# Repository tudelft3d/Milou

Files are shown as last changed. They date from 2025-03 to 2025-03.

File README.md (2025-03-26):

# Milou: a low-cost open-source line-following robot to study indoor air



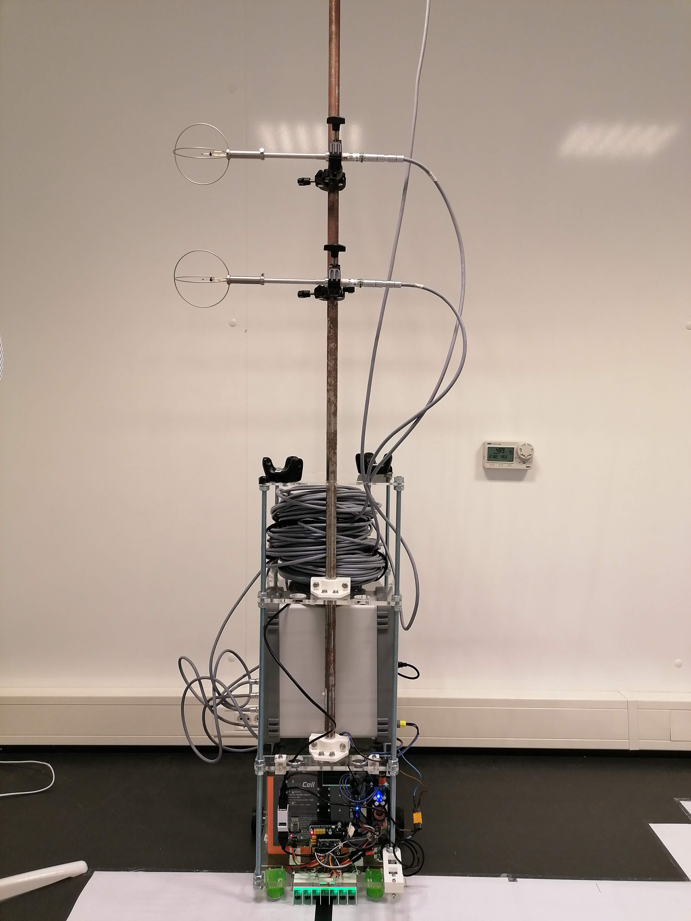
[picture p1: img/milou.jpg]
Milou


Milou is a low-cost line-following robot that automates indoor measurements with low interference. She follows a line and stops at sampling points to measure.
This repository contains the blueprints to build Milou, the code to run and operate it, and the code to post-process the data from a measurement campaign that we did.

This repository accompanies the paper [Milou: a low-cost open-source line-following robot to study indoor air](TO BE PUBLISHED).

## Description of directories

1. `building_milou`: contains the drawings to laser cut and 3d print all parts of Milou in `drawings`, the Arduino code needed to run Milou in `milou_line_following`, and the code needed to connect Milou to a computer remotely in `rp_to_mu_connection`.
2. `postprocessing`: contains three Python files that use the data from this [4TU repository](https://doi.org/10.4121/41307b71-2096-4a31-82ba-f523a18c109a). requirements.txt contains the dependencies to run the python code.

## Parts
The following is a list of all the parts we used to build Milou.
Equivalent parts are also possible.

| Parts 							| Quantity |
| --- 							| ---|
| Arduino Nano Every					| 1 |
| Raspberry Pi Zero W					| 1 |
| MG996R Servo motors 					| 2 |
| ⌀ 6 mm stainless steel rod (1 m long. Use it to make 2 13 cm shafts from motors to wheels) 		 				| 1 |
| 6 mm to 6 mm coupler 					| 2 |
| Ball bearing (⌀ 6 mm inner and ⌀ 19 mm outer) 					| 2 |
| 50 mm ⌀ Aluminum wheel (we needed two on each side to carry the weight)					| 4 |
| Heavy duty castor balls				| 2 |
| TCRT5000 Tracking Sensor Module 	| 7 |
| 12V LiFePO4 battery (38Ah)			| 1 |
| Switch button							| 1 |
| HC-06 Bluetooth module				| 1 |
| ⌀ 10 mm threaded stainless steel rod (1 m long)| 4 |
| ⌀ 20 mm hollow tube (1.75 m long)		| 1 |
| Step-down converter 12 V to 9V (200W)	| 1 |
| Step-down converter 12 V to 5V (5A)	| 2 |

And a lot of wires, screws, nuts, rings, and spacers.
We also used busbars to distribute the power from the battery to the various components.

The rest of the parts are laser cut or 3d printed (see drawings folder).

Below is the wiring scheme of Milou's electrical components.
Circuit board

## Acknowledgements
We want to acknowledge the following [Instructables](https://www.instructables.com/Line-Follower-Robot-PID-Control-Android-Setup/) post that helped build Milou.

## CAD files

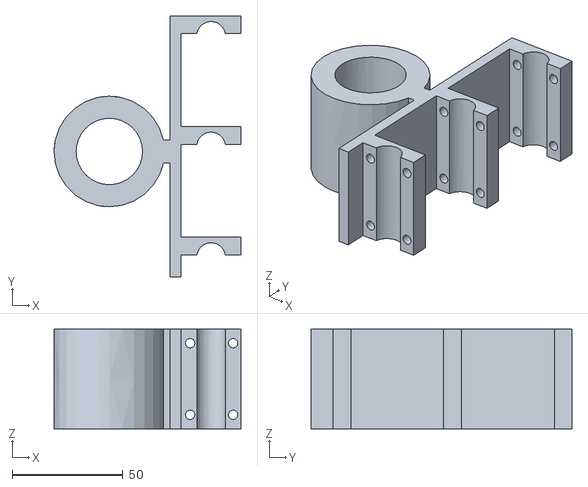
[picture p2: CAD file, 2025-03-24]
building_milou/drawings/probes_holder_bigger_handle.stl
84.5 x 118.0 x 45.0

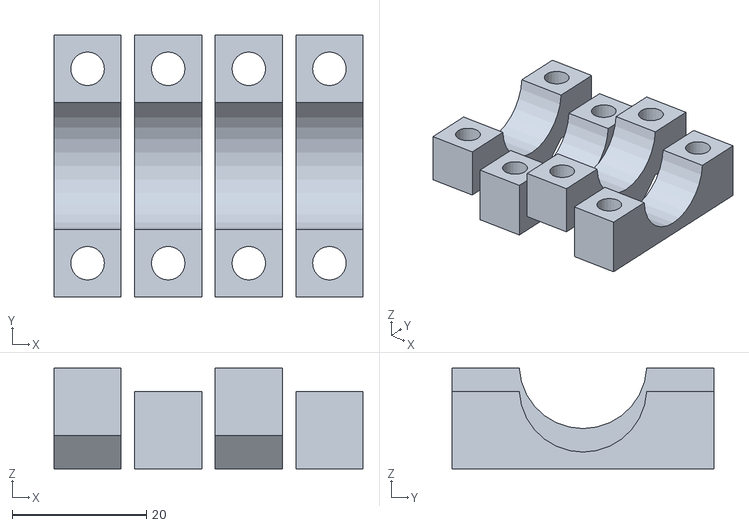
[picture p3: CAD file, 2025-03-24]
building_milou/drawings/pillow_block.stl
46.0 x 38.9 x 15.0

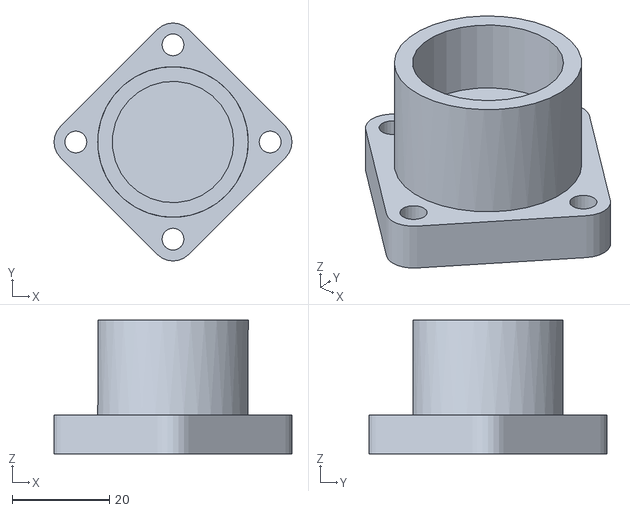
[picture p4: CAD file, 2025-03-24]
building_milou/drawings/case_castor_balls.stl
49.0 x 49.0 x 27.5

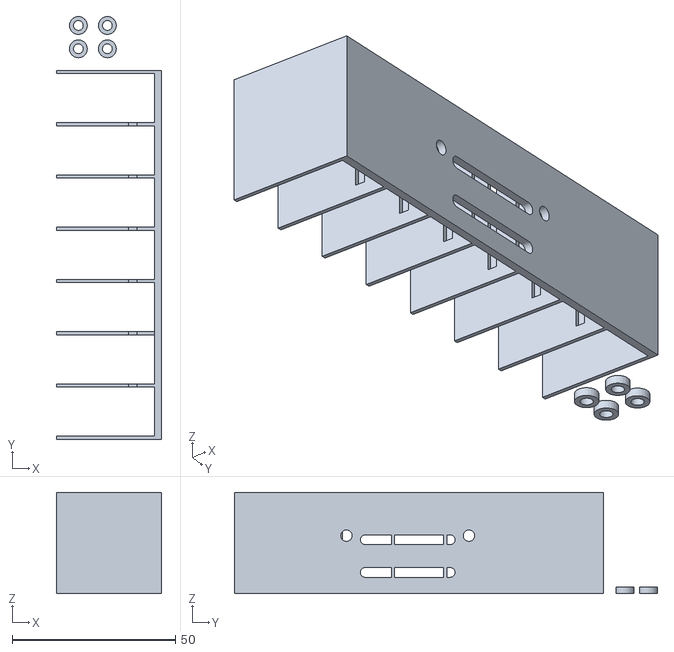
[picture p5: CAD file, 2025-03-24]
building_milou/drawings/newsensor3dprinting_white_02.stl
32.0 x 129.4 x 31.0

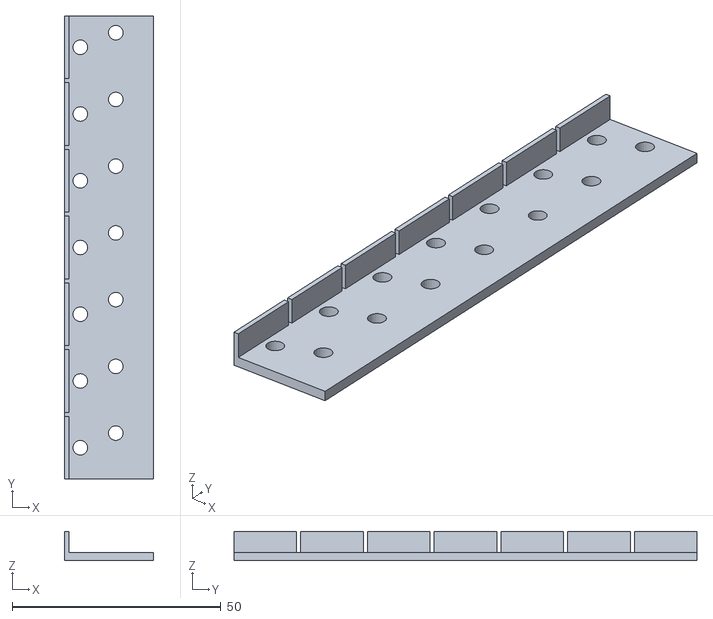
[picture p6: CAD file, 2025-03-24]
building_milou/drawings/newsensor3dprinting_transparent.stl
21.3 x 111.0 x 7.00

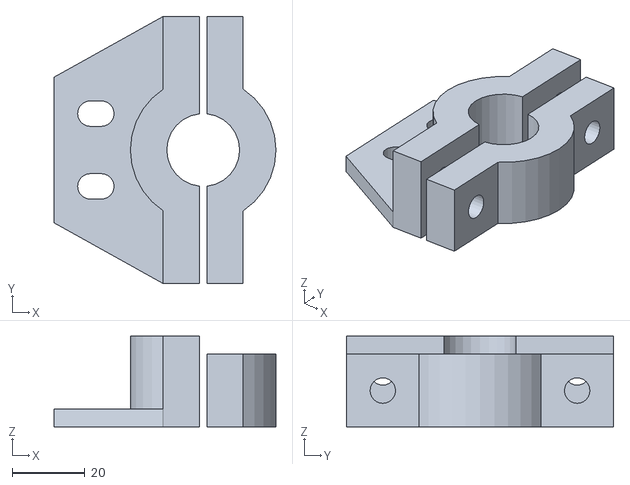
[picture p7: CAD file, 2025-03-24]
building_milou/drawings/bearing_pipe_custom.stl
61.0 x 73.4 x 25.0

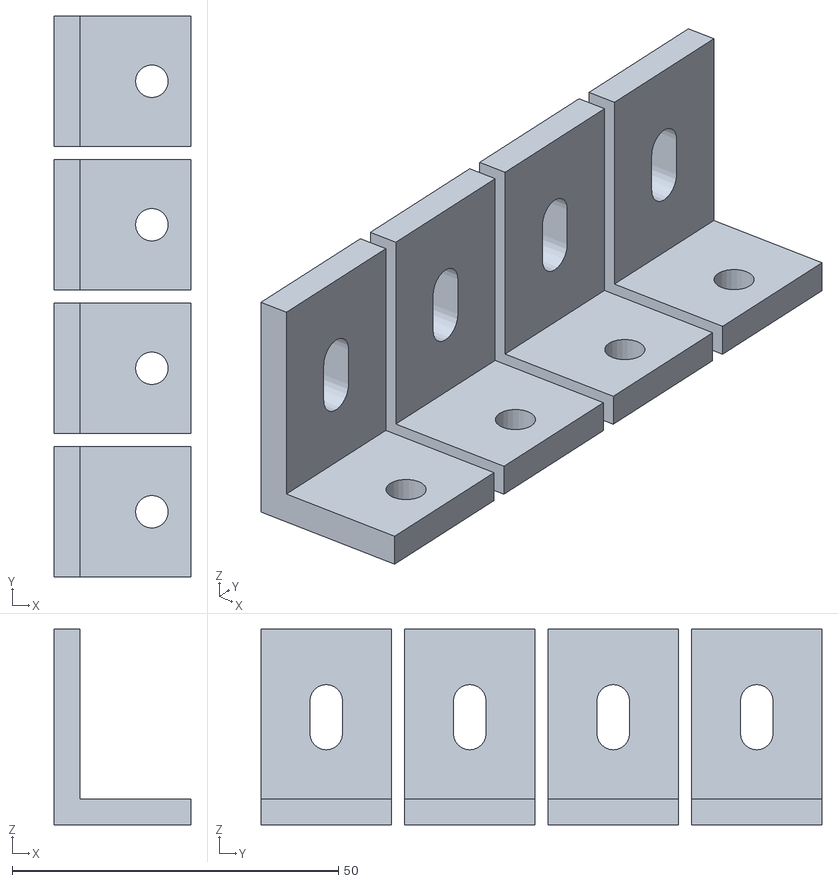
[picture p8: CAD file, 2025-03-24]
building_milou/drawings/L_3d_printing.stl
21.0 x 86.0 x 30.0

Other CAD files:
building_milou/drawings/laser_cut_4_mm.dwg
building_milou/drawings/laser_cut_8_mm.dwg

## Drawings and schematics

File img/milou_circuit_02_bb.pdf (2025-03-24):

W 103
DC009

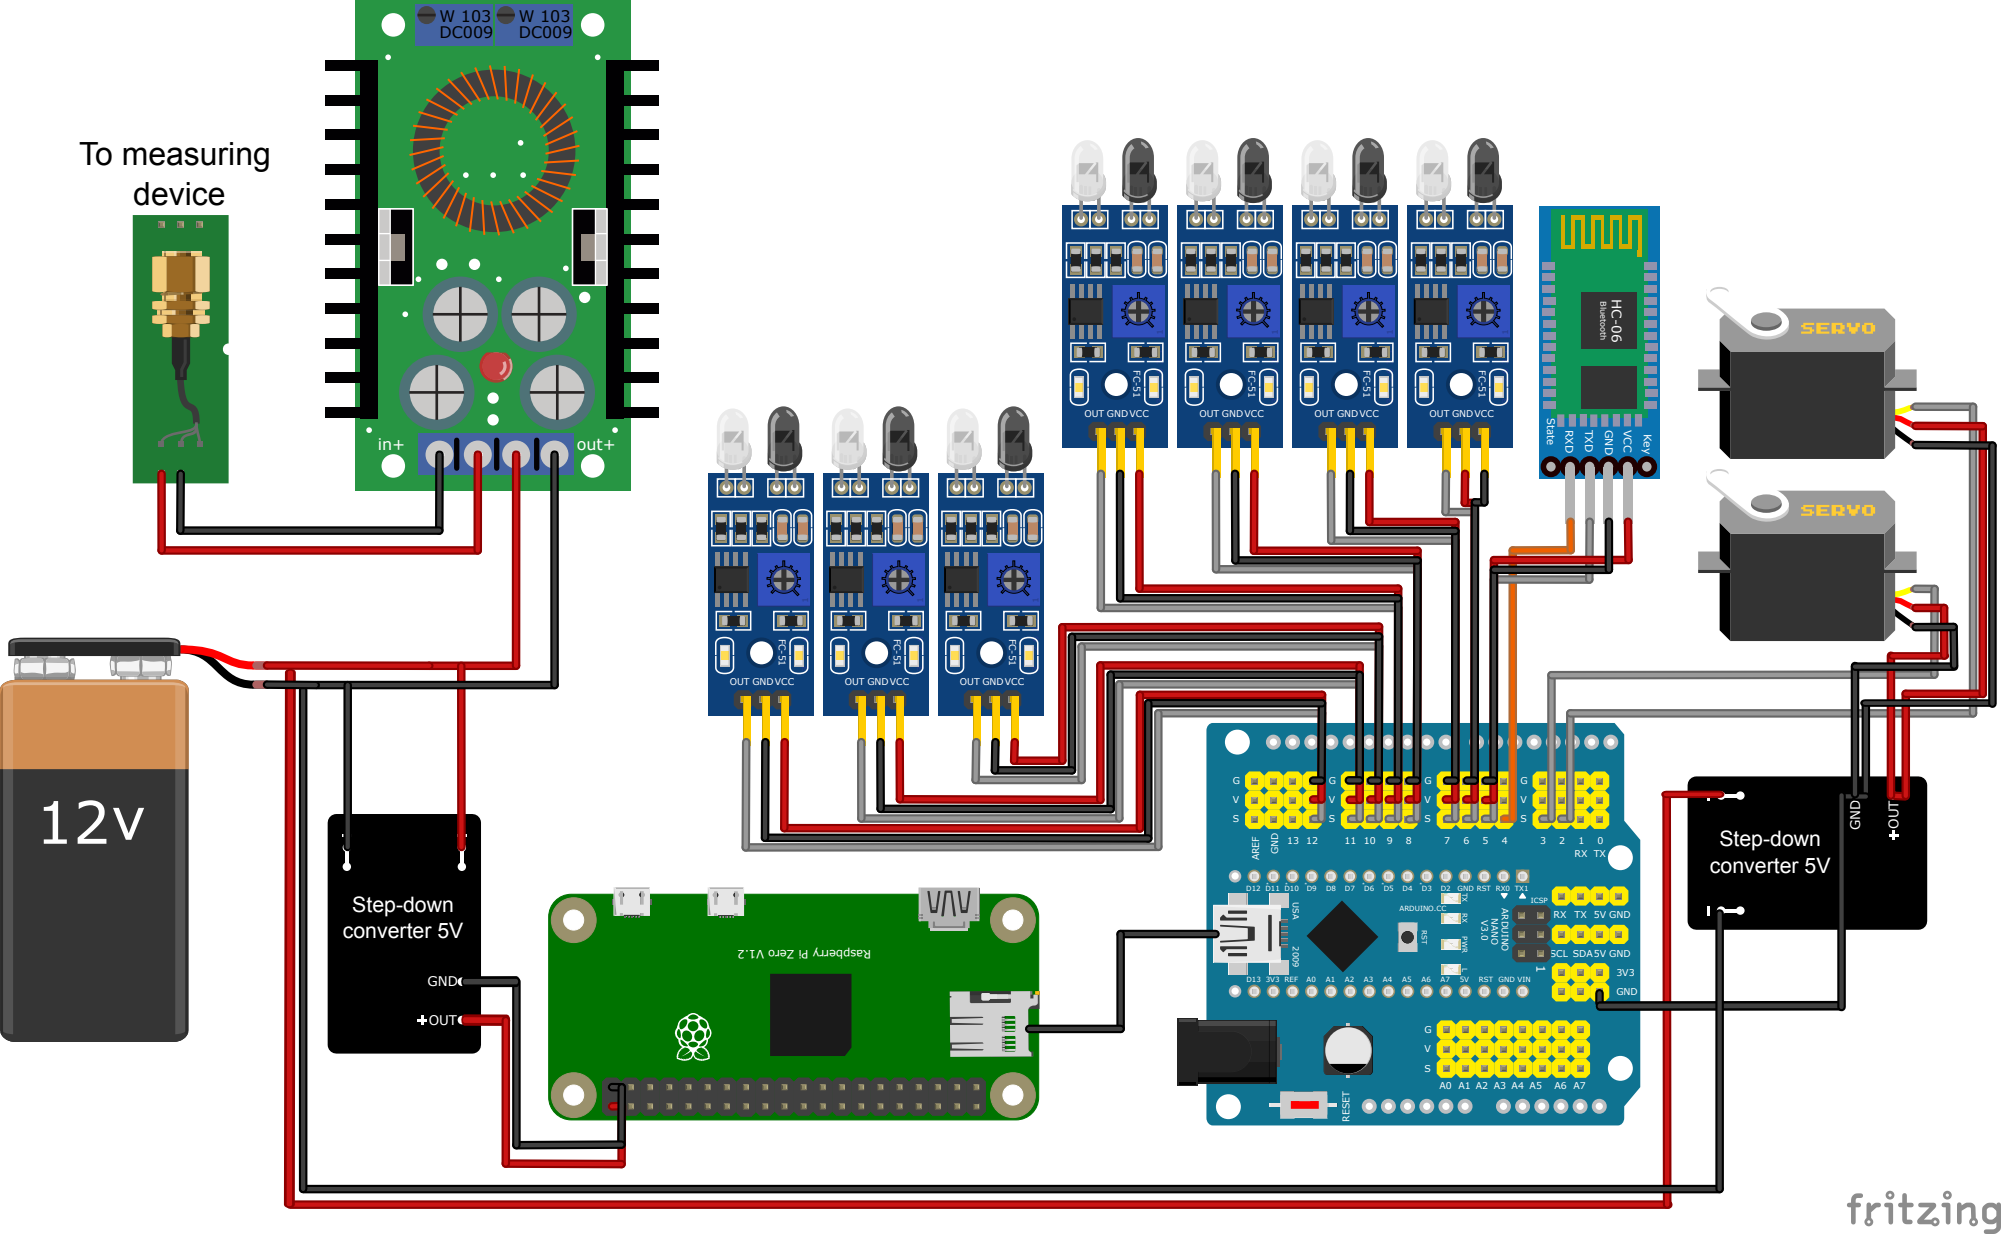
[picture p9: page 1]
Key; RXD; TXD; GND; VCC; State; Bluetooth; out+; OUT; RESET; SCL; GND5VSDA; GND5VTX; AREF; GND13 12 11 10 9 8 7 6 5 4 3 2 1 0 TXRX; GNDD2D3; TX1RX0RST; 1 ICSP; RST; 2009USA; ARDUINO.CC; ARDUINO; NANO; GNDOUT; Step-down converter 5V; To measuring device

TX RX PWR

D13 3V3 REF A0 A1 A2 A3 A4 A5 A6 A7 5V RST GND VIN

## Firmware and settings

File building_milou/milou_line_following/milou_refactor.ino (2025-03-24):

#include <Servo.h>
#include "definitions.h"

// LFSensor more to the Left is index "0"
int LFSensor[7]={0, 0, 0, 0, 0, 0, 0};
volatile bool run = false;

volatile char mode = 0;

// PID controller variables
float Kp=50; //12
float Ki=0;
float Kd=0; //20

float error=0, P=0, I=0, D=0, PIDvalue=0;
float previousError=0, previousI=0;

// Servo's
Servo leftServo;
Servo rightServo;

// BT Module
#include <SoftwareSerial.h>
SoftwareSerial BT1(4, 6);

// timer
unsigned long startTimer;

void setup() 
{ 
  Serial.begin(9600);
  BT1.begin(9600);
  
  // line follow sensors pin setup
  pinMode(farLeftSensor, INPUT);
  pinMode(lineFollowSensor0, INPUT);
  pinMode(lineFollowSensor1, INPUT);
  pinMode(lineFollowSensor2, INPUT);
  pinMode(lineFollowSensor3, INPUT);
  pinMode(lineFollowSensor4, INPUT);
  pinMode(farRightSensor, INPUT);
  
  // servo setup
  leftServo.attach(3);
  rightServo.attach(5);

  // initial mode
  mode = STOPPED;
  run = true;

  // wait for command to start operation
  while (mode==STOPPED) {
    checkBTcmd();  // verify if a comand is received from BT remote control
    manualCmd ();

    if(Serial.available()) {
      // Read the response from command centre
      int receivedData = Serial.parseInt();
      // Serial.print("Received data from command centre: ");
      // Check if the received data is 42
      if (receivedData == 1337) {
        // command centre sent back 42, exit while loop
        Serial.println("COMMENCING OPERATION");
        mode = FOLLOWING_LINE;
        break;
      }
    }
  }
}

void loop() 
{
  readLFSsensors();
  delay(100);

  if (!run) {
    motorStop();
    while (true) {}
  } else {
    switch (mode)
    {   
      case NO_LINE:
        // Make a 180 degree turn when we run out of line
        Serial.println("NO_LINE");
        motorStop(500);
        // motorTurnTimed180(LEFT);
        motorTurnAndFindLine(LEFT);
        break;
      
      case INTERSECTION:
        Serial.println("INTERSECTION");
        run=false;
        Serial.println("INTERSECTION STOP");
        break;
        
      case RIGHT_TURN:
        Serial.println("RIGHT_TURN");
        // check first if this is not a false detection of RIGHT_TURN
        run=false;
        Serial.println("UNEXPECTED MODE AFTER RIGHT_TURN");
        break;
        
      case LEFT_TURN:
        Serial.println("LEFT_TURN");
        run=false;
        Serial.println("UNEXPECTED MODE AFTER LEFT_TURN");
        break;
    
      case FOLLOWING_LINE:
        Serial.println("FOLLOWING_LINE");
        followLine();
        break;  

      case PAUSE_LINE:
        Serial.println("PAUSE_LINE");
        motorStop(5000);

        // Send a number from Arduino to command centre
        Serial.println("PAUSE_LINE SENDING MESSAGE");
        
        Serial.println(msgStartMeasurement);
        Serial.flush();

        // Wait for a response from command centre
        while (true) {
          if(Serial.available()) {
            // Read the response from command centre
            int receivedData = Serial.parseInt();
            // Serial.print("Received data from command centre: ");
            // Check if the received data is 42
            if (receivedData == 42) {
              // command centre sent back 42, exit while loop
              Serial.println("PAUSE_LINE RECEIVED COMMAND TO PROCEED");
              runExtraCentimetre();
              break;
            }
          }
        }
        break;

      default:
        Serial.println("UNKNOWN MODE");
        run = false;
    }
  }
}

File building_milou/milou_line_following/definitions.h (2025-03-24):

#define STOPPED 0
#define FOLLOWING_LINE 1
#define NO_LINE 2
#define INTERSECTION 3
// #define POS_LINE 4
#define RIGHT_TURN 5
#define LEFT_TURN 6
#define PAUSE_LINE 7

#define RIGHT -1
#define LEFT 1

// Line sensor pin configuration
const int farLeftSensor = 2; // No longer an Analog Pin
const int lineFollowSensor0 = 12; 
const int lineFollowSensor1 = 11; 
const int lineFollowSensor2 = 10; 
const int lineFollowSensor3 = 9;
const int lineFollowSensor4 = 8;
const int farRightSensor = 7; // No longer an Analog Pin

// Line - Void colour
const int line_reflectance=0;
const int void_reflectance=1;

// motor control constants
const int power = 200; // 125
const int iniMotorPower = 200; // 125
const int adjL = 0; // 100
const int adjR = 0; // 100
const float adjTurn = 950; // time factor for turns
const float adjTurn180 = 880; // time factor for 180 degree turns
const int extraInch = 1000;
const int extraCentimetre = 1300; // 1500
const int untilAxis = 2500;
const unsigned long carLength = 6900; //8000

const int msgStartMeasurement = 18;

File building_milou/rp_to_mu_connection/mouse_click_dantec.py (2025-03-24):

import pyautogui
import time

pyautogui.PAUSE = 0.5
pyautogui.useImageNotFoundException()


def test_mouse():
    pyautogui.moveTo(1750, 30, duration=0.5)
    pyautogui.click()
    # pyautogui.rightClick()


def comfortSense():
    while True:
        try:
            time.sleep(1)
            # Locate the center of the button
            x_location, y_location = pyautogui.locateCenterOnScreen('start_measurement_button.PNG')

            # Click the button
            pyautogui.click(x_location, y_location)
            pyautogui.moveTo(5, 5, duration=0.5)
            break
        except pyautogui.ImageNotFoundException:
            pass

    while True:
        try:
            time.sleep(1)
            pyautogui.locateOnScreen('start_measurement_button.PNG')
            break
        except pyautogui.ImageNotFoundException:
            pass


if __name__ == '__main__':
    # test_mouse()  # this is to minimise the pycharm window
    comfortSense()

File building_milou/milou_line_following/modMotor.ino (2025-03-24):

void motorStop(unsigned int time)
{
  leftServo.writeMicroseconds(1500);
  rightServo.writeMicroseconds(1500);
  delay(time);
}

void motorStop()
{
  motorStop(0);
}

//--------------------------------------------- 
void motorForward()
{
  leftServo.writeMicroseconds(1500 - (power+adjL));
  rightServo.writeMicroseconds(1500 + (power+adjR));
}

//---------------------------------------------
void motorBackward()
{
  leftServo.writeMicroseconds(1500 + power);
  rightServo.writeMicroseconds(1500 - power);
}

//---------------------------------------------
// void motorFwTime (unsigned int time)
// {
//   motorForward();
//   delay (time);
//   motorStop(200);
// }

// //---------------------------------------------
// void motorBwTime (unsigned int time)
// {
//   motorBackward();
//   delay (time);
//   motorStop(200);
// }

//------------------------------------------------
void motorTurn(int direction){
  leftServo.writeMicroseconds(1500 - (iniMotorPower+adjL)*direction);
  rightServo.writeMicroseconds(1500 - (iniMotorPower+adjR)*direction);
}

void motorTurnTimed(int direction, int degrees, float timeFactor)
{
  motorTurn(direction);
  delay(round(timeFactor*(degrees/10)));
  motorStop();
}

void motorTurnTimed(int direction, int degrees)
{
  motorTurnTimed(direction, degrees, adjTurn);
}

void motorTurnTimed180(int direction)
{
  motorTurnTimed(direction, 180, adjTurn180);
}

void motorTurnAndFindLine(int direction)
{
  motorTurn(direction);
  while(!LFS_middle()) {

  }
  motorStop();
}

void turnLeft() {
  Serial.println("PREPARE LEFT TURN");
  followLineForCarLength();
  Serial.println("TURN 20 deg");
  motorTurnTimed(LEFT, 20);
  Serial.println("TURN TO LINE");
  motorTurnAndFindLine(LEFT);
}

//---------------------------------------------------
void motorPIDcontrol()
{
  
  int leftMotorSpeed = 1500 - (iniMotorPower+adjL) - PIDvalue;
  int rightMotorSpeed = 1500 + (iniMotorPower+adjR) - PIDvalue;
  
  // The motor speed should not exceed the max PWM value
  leftMotorSpeed = constrain(leftMotorSpeed, 1000, 2000);
  rightMotorSpeed = constrain(rightMotorSpeed, 1000, 2000);
  
  leftServo.writeMicroseconds(leftMotorSpeed);
  rightServo.writeMicroseconds(rightMotorSpeed);
  
  //Serial.print (PIDvalue);
  //Serial.print (" ==> Left, Right:  ");
  //Serial.print (leftMotorSpeed);
  //Serial.print ("   ");
  //Serial.println (rightMotorSpeed);
}

//---------------------------------------------------
void motorGoForward()
{
  
  int leftMotorSpeed = 1500 - (iniMotorPower);
  int rightMotorSpeed = 1500 + (iniMotorPower);
  
  // The motor speed should not exceed the max PWM value
  // constrain(leftMotorSpeed, 1000, 2000);
  // constrain(rightMotorSpeed, 1000, 2000);
  
  leftServo.writeMicroseconds(leftMotorSpeed);
  rightServo.writeMicroseconds(rightMotorSpeed);
}

//---------------------------------------------------
void runExtraInch(void)
{
  motorPIDcontrol();
  delay(extraInch);
  // motorStop(5000);
}

//---------------------------------------------------
void runExtraHalfInch(void)
{
  motorPIDcontrol();
  delay(extraInch/2);
  // motorStop(5000);
}

//---------------------------------------------------
void runExtraQuarterInch(void)
{
  motorPIDcontrol();
  delay(extraInch/4);
  // motorStop(5000);
}

//---------------------------------------------------
void runUntilAxis(void)
{
  motorGoForward();
  delay(untilAxis);
  // motorStop(5000);
}

//---------------------------------------------------
void runExtraCentimetre(void)
{
  motorGoForward();
  delay(extraCentimetre);
}

//---------------------------------------------------
void goAndTurn(int direction, int degrees)
{
  motorPIDcontrol(); // motorGoForward
  delay(carLength);
  motorTurnTimed(direction, degrees);
}
